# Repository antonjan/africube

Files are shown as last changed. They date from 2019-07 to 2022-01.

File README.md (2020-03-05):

# africube is the repository of a linear satellite transponder. (AMSATSA)
# pcb
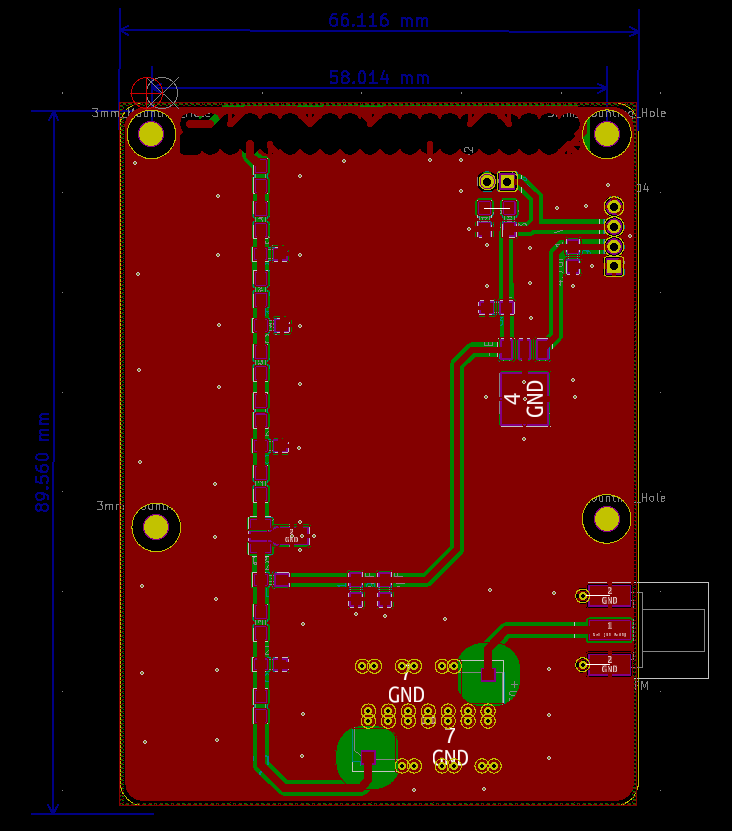
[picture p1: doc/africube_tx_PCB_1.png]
2220mW tx Board for Raspberry Pi 220mw 2m band board
<br>
# Project Status.
This project TX PCB is compleet and testing will start now. 10 September 2019
Transponder is now working propely and CW and APRS telemetry is also working.
Oustanding is sensor reading. 16 Jan 2020
# Link Budget

It is necessary that our beacon’s signal be able to reach the antenna at our ground station.  
The beacon will transmit at 145.850 MHz.<br>  
Using the free space model, we can calculate the maximum path loss:<br>
### Maximum Path Loss = 32.4 dB + 20 log(dkm) dB + 20 log(fMHz) dB=32.4 dB + 20 log(8000) dB + 20 log(140) dB=144.86 dB<br>
Our transmission power will be 200 mW, which in dBm is 23 (30 + 10 log(0.1)) <br>
The feeder loss for ourtransmitter will be quite low, since the radio is close to the antenna on the cubeSAT. <br>
We will assume this loss is about 0.2 dB and that the antenna’s gain is about 2 dI (which is reasonable for a whip antenna ona cubeSAT), so our effective isotropic radiated power should be about 24.6 dBm <br>
### EIRP = Transmission Power−Feeder Loss + Antenna Gain=23 dB−0.2 dB + 2 dB=25.8 dB<br>
To calculate the quality of our received signal we also need to know the polarization mismatch, the ionosphericpropagation mismatch, the antenna’s gain, the antenna’s feeder loss, and the noise floor.<br>
We will let thesebe 3 dB, 1 dB, 12.34 dBI, 5.5 dB, and−130 dBm, respectively.<br>
### Max Range Received Signal =  EIRP−Max Path Loss−Mismatch Loss − Propagation Loss +Antenna Gain−Feeder Loss= 25.8dB − 144.86 dB−3 dB−1 dB + 12.34 dB−5.5 dB=−117.22 dB<br>
### Quality Assessment    =    Max Range Received Signal−Noise Floor=−120.22 dB−(−130 dB)=    12.78 dBSo, at the ground station, we should expect a SNR of about 9.78 dB.<br>

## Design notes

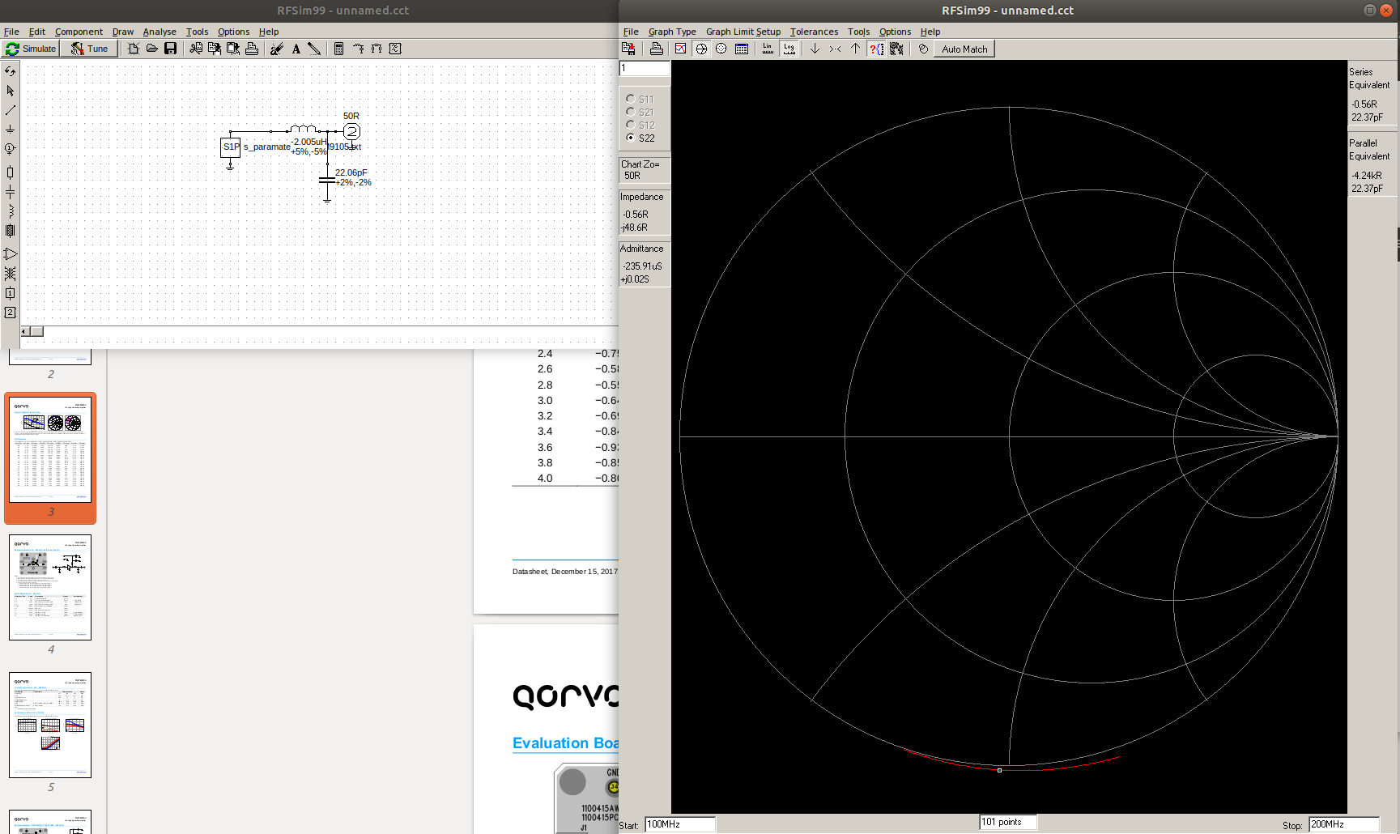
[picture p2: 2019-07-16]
doc/s_paramater_TQP7M9105_output_matching_1.png

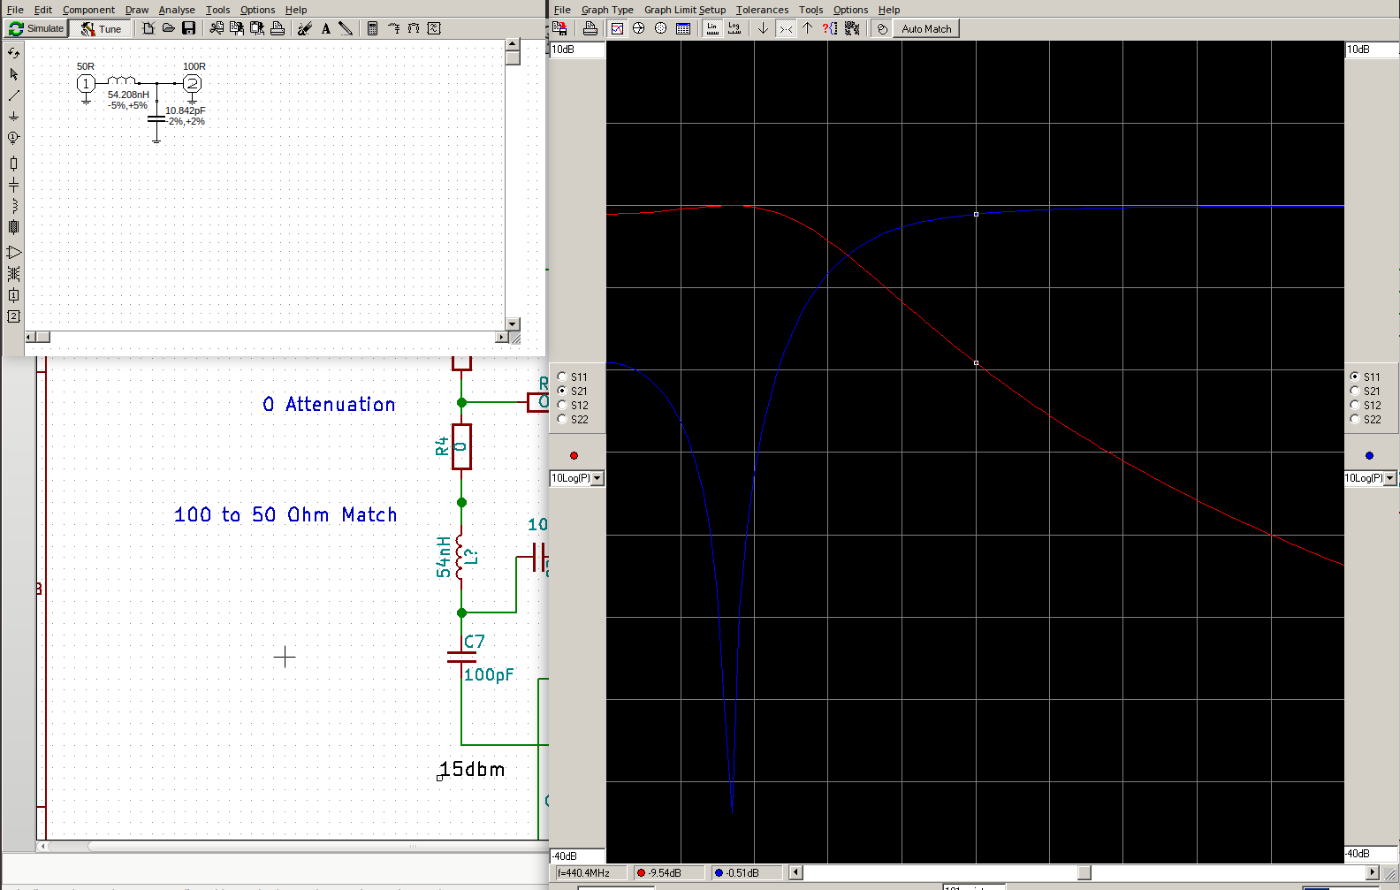
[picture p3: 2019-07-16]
doc/100_50_Ohm_matching_145.8Mhz.png

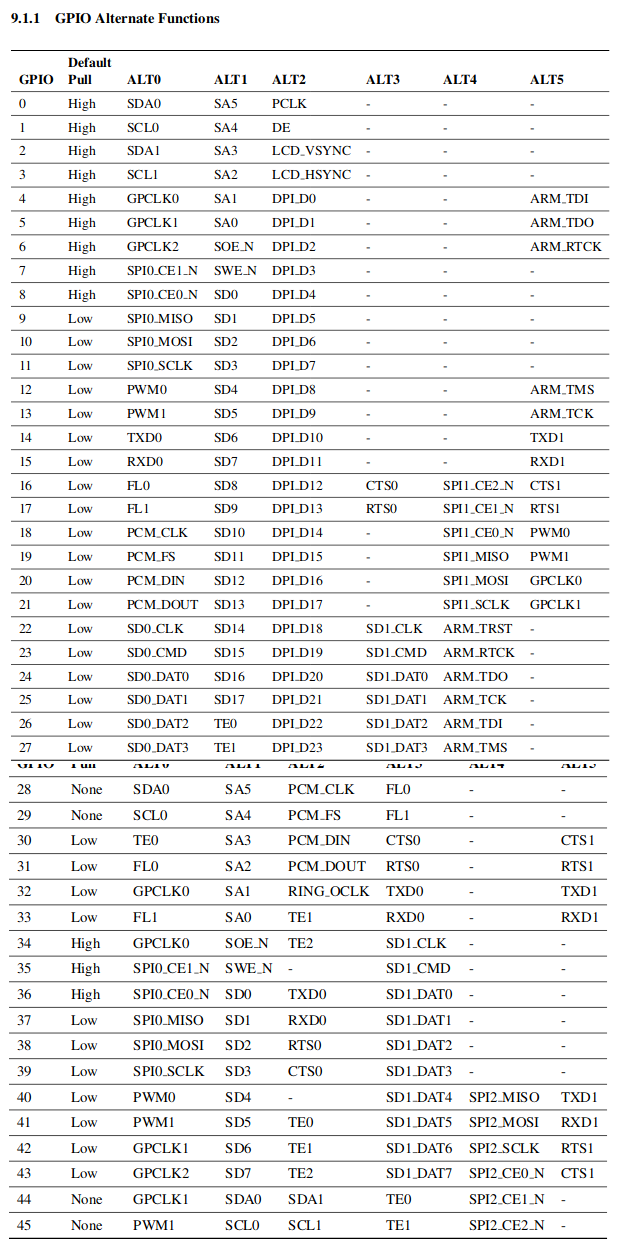
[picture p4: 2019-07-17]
doc/Raspberry_pi_Compute_Module_IO_pins_1.png

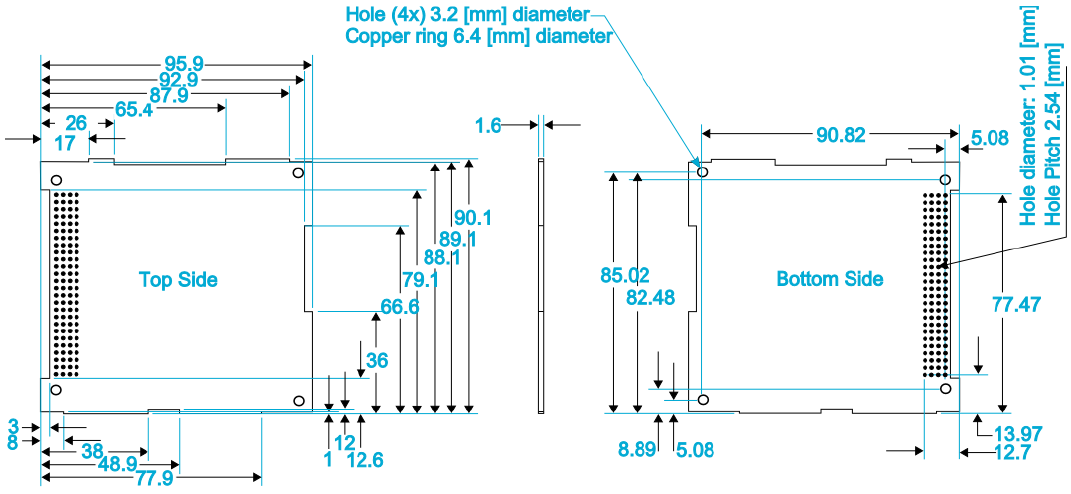
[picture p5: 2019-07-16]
doc/KletskousPCBOutline20160719.PNG

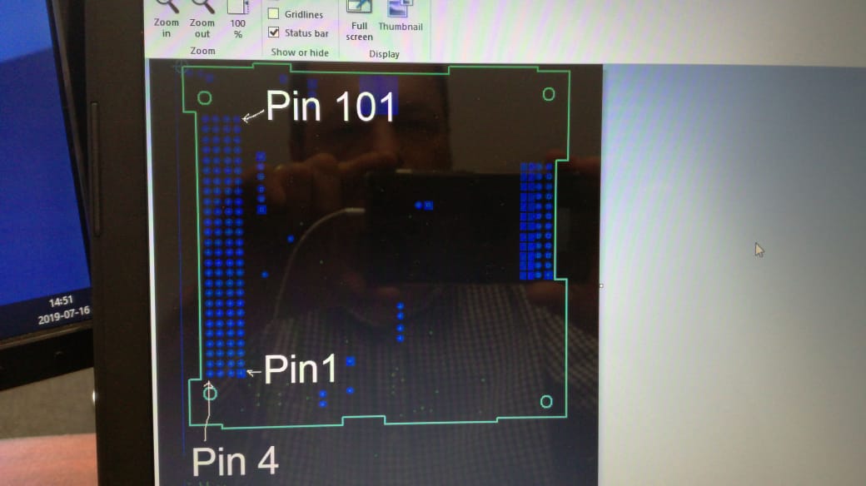
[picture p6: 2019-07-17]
doc/PC104_pin_configeration.jpeg

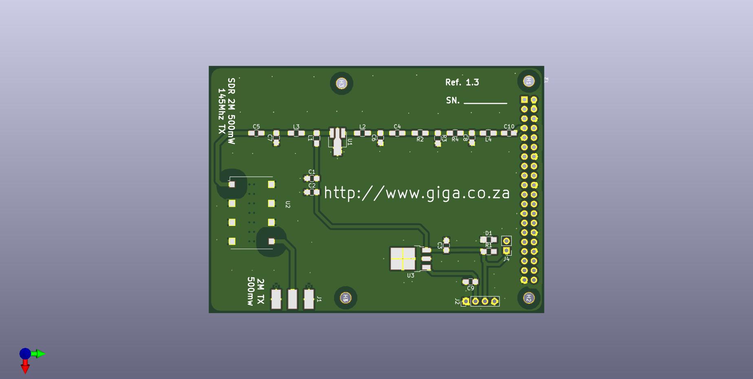
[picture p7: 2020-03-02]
africube3.jpg

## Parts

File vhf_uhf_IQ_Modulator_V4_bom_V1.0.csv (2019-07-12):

Component | Description | Part | References | Value | Footprint | Quantity Per PCB | Datasheet
1 | Unpolarized capacitor | C_Small | C27 | 100nF | C_0805_HandSoldering | 1
2 | Unpolarized capacitor | C_Small | C16 C21 | 100pF | C_0805_HandSoldering | 2
3 | Polarised capacitor | CP_Small | C5 C8 C23 C25 C28 | 10uF 16V | C_0805_HandSoldering | 5
4 | Unpolarized capacitor | C_Small | C24 | 15pF | C_0805_HandSoldering | 1
5 | Unpolarized capacitor | C_Small | C9 C14 | 1nF | C_0805_HandSoldering | 2
6 | Polarised capacitor | CP | C1 C13 | 1uF 16V | CP_Tantalum_Case-R_EIA-2012-12_Reflow | 2
7 | Polarised capacitor | CP_Small | C2 C3 C15 C17 C20 | 1uF 16V | CP_Tantalum_Case-R_EIA-2012-12_Reflow | 5
8 | Unpolarized capacitor | C_Small | C6 C7 C11 C12 | 2200pF | C_0805_HandSoldering | 4
9 | Unpolarized capacitor | C_Small | C19 C26 | 220pF | C_0805_HandSoldering | 2
10 | Unpolarized capacitor | C_Small | C18 | 27pF | C_0805_HandSoldering | 1
11 | Unpolarized capacitor | C_Small | C4 | 3.3pF | C_0805_HandSoldering | 1
12 | Unpolarized capacitor | C_Small | C22 C29 C30 C31 | 33pF | C_0805_HandSoldering | 4
13 | Polarised capacitor | CP_Small | C10 | 4.7uF 16V | C_0805_HandSoldering | 1
14 | 3-pin audio jack receptable (stereo/TRS connector) | Audio-Jack-3 | J3 | Audio-Jack-3 | Pin_Header_Straight_1x03_Pitch2.54mm | 1
15 |  | CONN_01X03 | J1 | CONN_01X03 | Pin_Header_Straight_1x03_Pitch2.54mm | 1
16 | Generic connector, single row, 01x04 | Conn_01x04 | J4 | CONN_01X04 | Pin_Header_Straight_1x04_Pitch2.54mm | 1
17 | coaxial connector (BNC, SMA, SMB, SMC, Cinch/RCA, ...) | Conn_Coaxial | J5 | SMA Edge FM | Molex_SMA_Jack_Edge_Mount | 1
18 | point | TEST_1P | J2 | TEST_1P | Pin_Header_Straight_1x01_Pitch2.54mm | 1
19 | Inductor | L | L7 L8 | 110nH | L_0805_HandSoldering | 2
20 | Inductor | L | L3 | 22nF | C_0805_HandSoldering | 1
21 | Inductor | L | L1 L5 | 33nF | C_0805_HandSoldering | 2
22 | Inductor | L | L2 L4 | 33nH | L_0805_HandSoldering | 2
23 | Inductor | L | L6 L9 | 56nH | L_0805_HandSoldering | 2
24 |  | BC817-40 | Q1 Q2 Q3 | BC817-40 | SOT-23 | 3
25 | Resistor | R | R9 R12 | 0 | R_0805_HandSoldering | 2
26 | Resistor | R | R1 R13 | 10k | R_0805_HandSoldering | 2
27 | Resistor | R | R2 R3 R5 R6 | 1K | R_0805_HandSoldering | 4
28 | Resistor | R | R4 | 1k8 | R_0805_HandSoldering | 1
29 | Resistor | R | R10 | 2k2 | R_0805_HandSoldering | 1
30 | Resistor | R | R17 | 4k7 | R_0805_HandSoldering | 1
31 | Resistor | R | R15 R16 | 6k5 | R_0805_HandSoldering | 2
32 | Resistor | R | R7 R8 R14 | 6k8 | R_0805_HandSoldering | 3
33 | Resistor | R | R11 | OC | R_0805_HandSoldering | 1
34 | Potentiometer | POT | RV1 RV2 | 4k7 | Potentiometer_Bourns_3314G_Vertical | 2
35 |  | MCP3421A0T-E/CH-RESCUE-vhf_uhf_IQ_Modulator | U5 | MCP3421A0T-E/CH | SOT-23-6_Handsoldering | 1
36 |  | MMZ09332BT1 | U2 | MMZ09332BT1 | QFN-12-1EP_3x3mm_P0.5mm_EP1.65x1.65mm | 1
37 |  | orange_pi_zero | U4 | Orange Pi zero | orangepi-zero | 1
38 |  | Si570 | U3 | Si570 | Oscillator_SMD_SI570_SI571_HandSoldering | 1
39 |  | TRF3701 | U1 | TRF3701 | VQFN-16_3x3mm_trf3701_new | 1
Component Groups: | 39
Component Count: | 72
Fitted Components: | 72
Number of PCBs: | 1
Total components: | 72
Schematic Version: | V1.0
Schematic Date: | 2018-06-01
BoM Date: | Fri 03 Aug 2018 14:08:11 SAST
Schematic Source: | /home/anton/Documents/kicad/IQ_Modulator/vhf_uhf_IQ_Modulator_V4.sch
KiCad Version: | Eeschema 4.0.7-e2-6376~61~ubuntu18.04.1

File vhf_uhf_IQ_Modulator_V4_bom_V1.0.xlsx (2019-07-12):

Component | Description | Part | References | Value | Footprint | Quantity Per PCB | Datasheet | Manufacturer Part Number
1 | Unpolarized capacitor | C_Small | C27 | 100nF | C_0805_HandSoldering | 1 |  | 587-1134-1-ND
2 | Unpolarized capacitor | C_Small | C16 C21 | 100pF | C_0805_HandSoldering | 2 |  | 08052U101JAT2A
3 | Polarised capacitor | CP_Small | C5 C8 C23 C25 C28 | 10uF 16V | C_0805_HandSoldering | 5 |  | 478-8115-1-ND
4 | Unpolarized capacitor | C_Small | C24 | 15pF | C_0805_HandSoldering | 1 |  | 1276-2585-1-ND
5 | Unpolarized capacitor | C_Small | C9 C14 | 1nF | C_0805_HandSoldering | 2 |  | 399-16591-1-ND
6 | Polarised capacitor | CP | C1 C13 | 1uF 16V | CP_Tantalum_Case-R_EIA-2012-12_Reflow | 2 |  | 478-3346-1-ND
7 | Polarised capacitor | CP_Small | C2 C3 C15 C17 C20 | 1uF 16V | CP_Tantalum_Case-R_EIA-2012-12_Reflow | 5 |  | 478-3346-1-ND
8 | Unpolarized capacitor | C_Small | C6 C7 C11 C12 | 2200pF | C_0805_HandSoldering | 4 |  | 311-3619-1-ND
9 | Unpolarized capacitor | C_Small | C19 C26 | 220pF | C_0805_HandSoldering | 2 |  | 490-6104-1-ND
10 | Unpolarized capacitor | C_Small | C18 | 27pF | C_0805_HandSoldering | 1 |  | 478-3844-1-ND
11 | Unpolarized capacitor | C_Small | C4 | 3.3pF | C_0805_HandSoldering | 1 |  | 478-3846-1-ND
12 | Unpolarized capacitor | C_Small | C22 C29 C30 C31 | 33pF | C_0805_HandSoldering | 4 |  | 478-10472-1-ND
13 | Polarised capacitor | CP_Small | C10 | 4.7uF 16V | C_0805_HandSoldering | 1 |  | 478-8125-1-ND
14 | 3-pin audio jack receptable (stereo/TRS connector) | Audio-Jack-3 | J3 | Audio-Jack-3 | Pin_Header_Straight_1x03_Pitch2.54mm | 1 |  | ED7264-03-ND
15 |  | CONN_01X03 | J1 | CONN_01X03 | Pin_Header_Straight_1x03_Pitch2.54mm | 1 |  | ED7264-03-ND
16 | Generic connector, single row, 01x04 | Conn_01x04 | J4 | CONN_01X04 | Pin_Header_Straight_1x04_Pitch2.54mm | 1 |  | Digi-Key Part Number ED7264-04-ND
17 | coaxial connector (BNC, SMA, SMB, SMC, Cinch/RCA, ...) | Conn_Coaxial | J5 | SMA Edge FM | Molex_SMA_Jack_Edge_Mount | 1 |  | CON-SMA-EDGE-S-ND
18 | point | TEST_1P | J2 | TEST_1P | Pin_Header_Straight_1x01_Pitch2.54mm | 1 |  | ED7264-01-ND
19 | Inductor | L | L7 L8 | 110nH | L_0805_HandSoldering | 2 |  | 490-5665-1-ND
20 | Inductor | L | L3 | 22nH | C_0805_HandSoldering | 1 |  | CE201210-22NJCT-ND
21 | Inductor | L | L1 L5 | 33nH | C_0805_HandSoldering | 2 |  | 732-8077-1-ND
22 | Inductor | L | L2 L4 | 33nH | L_0805_HandSoldering | 2 |  | 490-5655-1-ND
23 | Inductor | L | L6 L9 | 56nH | L_0805_HandSoldering | 2 |  | 490-5660-1-ND
24 |  | BC817-40 | Q1 Q2 Q3 | BC817-40 | SOT-23 | 3 |  | BC817-40-TPMSCT-ND
25 | Resistor | R | R9 R12 | 0 Ohm | R_0805_HandSoldering | 2 |  | MCU0805-0.0-ZZCT-ND
26 | Resistor | R | R1 R13 | 10k | R_0805_HandSoldering | 2 |  | RNCP0805FTD10K0CT-ND
27 | Resistor | R | R2 R3 R5 R6 | 1K | R_0805_HandSoldering | 4 |  | 36-5110CT-ND
28 | Resistor | R | R4 | 1k8 | R_0805_HandSoldering | 1 |  | RNCP0805FTD10K0CT-ND
29 | Resistor | R | R10 | 2k2 | R_0805_HandSoldering | 1 |  | RMCF0805JT1K80CT-ND
30 | Resistor | R | R17 | 4k7 | R_0805_HandSoldering | 1 |  | 696-1387-1-ND
31 | Resistor | R | R15 R16 | 6k5(6k8) | R_0805_HandSoldering | 2 |  | 311-6.80KCRCT-ND
32 | Resistor | R | R7 R8 R14 | 6k8 | R_0805_HandSoldering | 3 |  | 311-6.80KCRCT-ND
33 | Resistor | R | R11 | OC | R_0805_HandSoldering | 1 |  | No Connection
34 | Potentiometer | POT | RV1 RV2 | 4k7 | Potentiometer_Bourns_3314G_Vertical | 2 |  | 3314J-1-472ECT-ND
35 |  | MCP3421A0T-E/CH-RESCUE-vhf_uhf_IQ_Modulator | U5 | MCP3421A0T-E/CH | SOT-23-6_Handsoldering | 1 |  | MCP3421A0T-E/CHCT-ND
36 |  | MMZ09332BT1 | U2 | MMZ09332BT1 | QFN-12-1EP_3x3mm_P0.5mm_EP1.65x1.65mm | 1 |  | MMZ09332BT1DKR-ND
37 |  | orange_pi_zero | U4 | Orange Pi zero | orangepi-zero | 1
38 |  | Si570 | U3 | Si570 | Oscillator_SMD_SI570_SI571_HandSoldering | 1 |  | 336-3900-ND
39 |  | TRF3701 | U1 | TRF3701 | VQFN-16_3x3mm_trf3701_new | 1 |  | 296-17198-ND
Component Groups: | 39
Component Count: | 72
Fitted Components: | 72
Number of PCBs: | 1
Total components: | 72
Schematic Version: | V1.0
Schematic Date: | 2018-06-01
BoM Date: | Fri 03 Aug 2018 14:08:11 SAST
Schematic Source: | /home/anton/Documents/kicad/IQ_Modulator/vhf_uhf_IQ_Modulator_V4.sch
KiCad Version: | Eeschema 4.0.7-e2-6376~61~ubuntu18.04.1

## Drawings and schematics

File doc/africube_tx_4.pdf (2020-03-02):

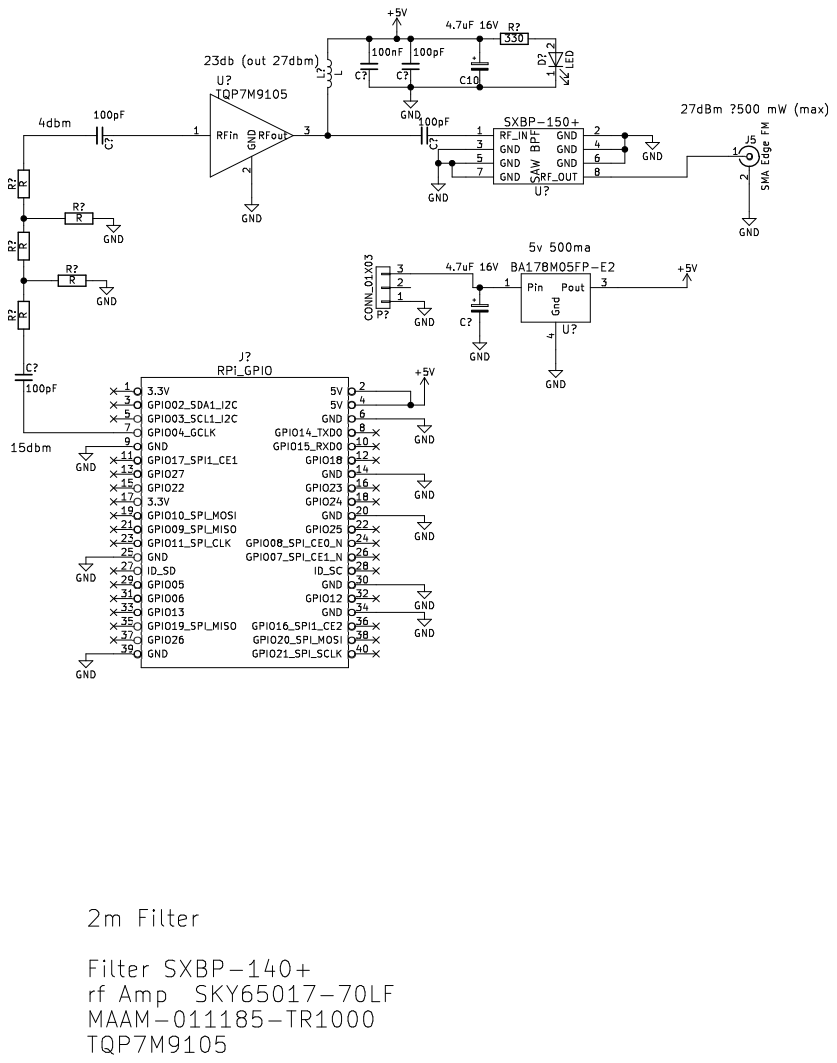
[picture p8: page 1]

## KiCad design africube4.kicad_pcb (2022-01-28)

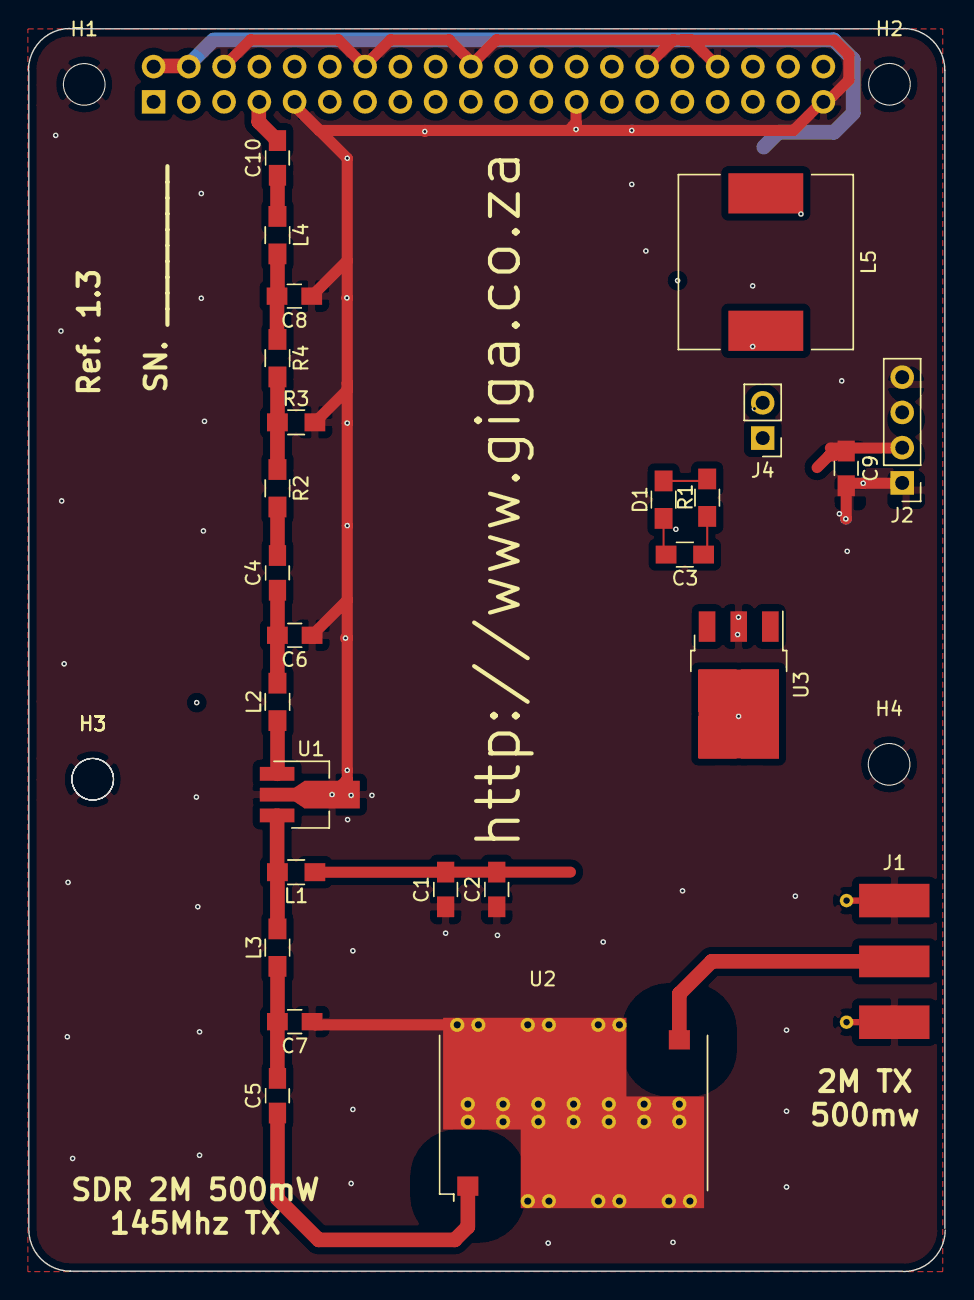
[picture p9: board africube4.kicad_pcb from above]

Board: 2 copper layers, 66.1 x 89.6 mm, 34 parts (0 on the bottom side), 16 nets.

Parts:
C1: 100nF; C_0805_HandSoldering
C2, C4, C5, C10: 100pF; C_0805_HandSoldering
C3: OC; R_0805_HandSoldering
C6: 12pF; C_0805_HandSoldering
C7: 22pF; C_0805_HandSoldering
C8: 10pF; C_0805_HandSoldering
C9: 4.7uF 16V; C_0805_HandSoldering
D1: LED; R_0805_HandSoldering
H1, H2, H3, H3#2, H3#3, H3#4, H4: 3mm_hole; MountingHole_3mm
J1: SMA Edge FM; Molex_SMA_Jack_Edge_Mount
J2: Conn_01x04; Socket_Strip_Straight_1x04_Pitch2.54mm
J3: RPi_GPIO; PinSocket_2x20_P2.54mm_Vertical
J4: Conn_01x02; Pin_Header_Straight_1x02_Pitch2.54mm
L1: 12nH; R_0805_HandSoldering
L2, L3, L4: 0; R_0805_HandSoldering
L5: 0; L_12x12mm_H8mm
R1, R3: OC; R_0805_HandSoldering
R2, R4: 0; R_0805_HandSoldering
U1: TQP7M9105; SOT-89-3_Handsoldering
U2: SXBP-150+; Mini-Circuits_HF1139_LandPatternPL-230
U3: BA178M05FP-E2; TO-252-3_TabPin4

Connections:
+5V: C1.2, C2.2, J2.3, L1.1, U3.3
GND: C1.1, C2.1, C6.1, C7.1, C8.1, C9.2, H1.1, H2.1, H3.1, H3#2.1, H3#3.1, H3#4.1, H4.1, J1.2, J2.1, J2.4, J3.6, J3.9, J3.14, J3.20, J3.25, J3.30, J3.34, J3.39, R3.2, U1.2, U2.2, U2.3, U2.4, U2.5, U2.6, U2.7, U3.2, U3.4
unnamed: C4.1, C6.2, L2.2
unnamed: C4.2, R2.2
unnamed: C5.1, U2.1
unnamed: C5.2, C7.2, L3.1
unnamed: C8.2, L4.2, R4.1
unnamed: C9.1, J2.2, U3.1
unnamed: C10.1, L4.1
unnamed: C10.2, J3.7
unnamed: J1.1, U2.8
unnamed: J3.2, J3.4, L5.1
unnamed: J4.2, L5.2
unnamed: L1.2, L3.2, U1.3
unnamed: L2.1, U1.1
unnamed: R2.1, R3.1, R4.2

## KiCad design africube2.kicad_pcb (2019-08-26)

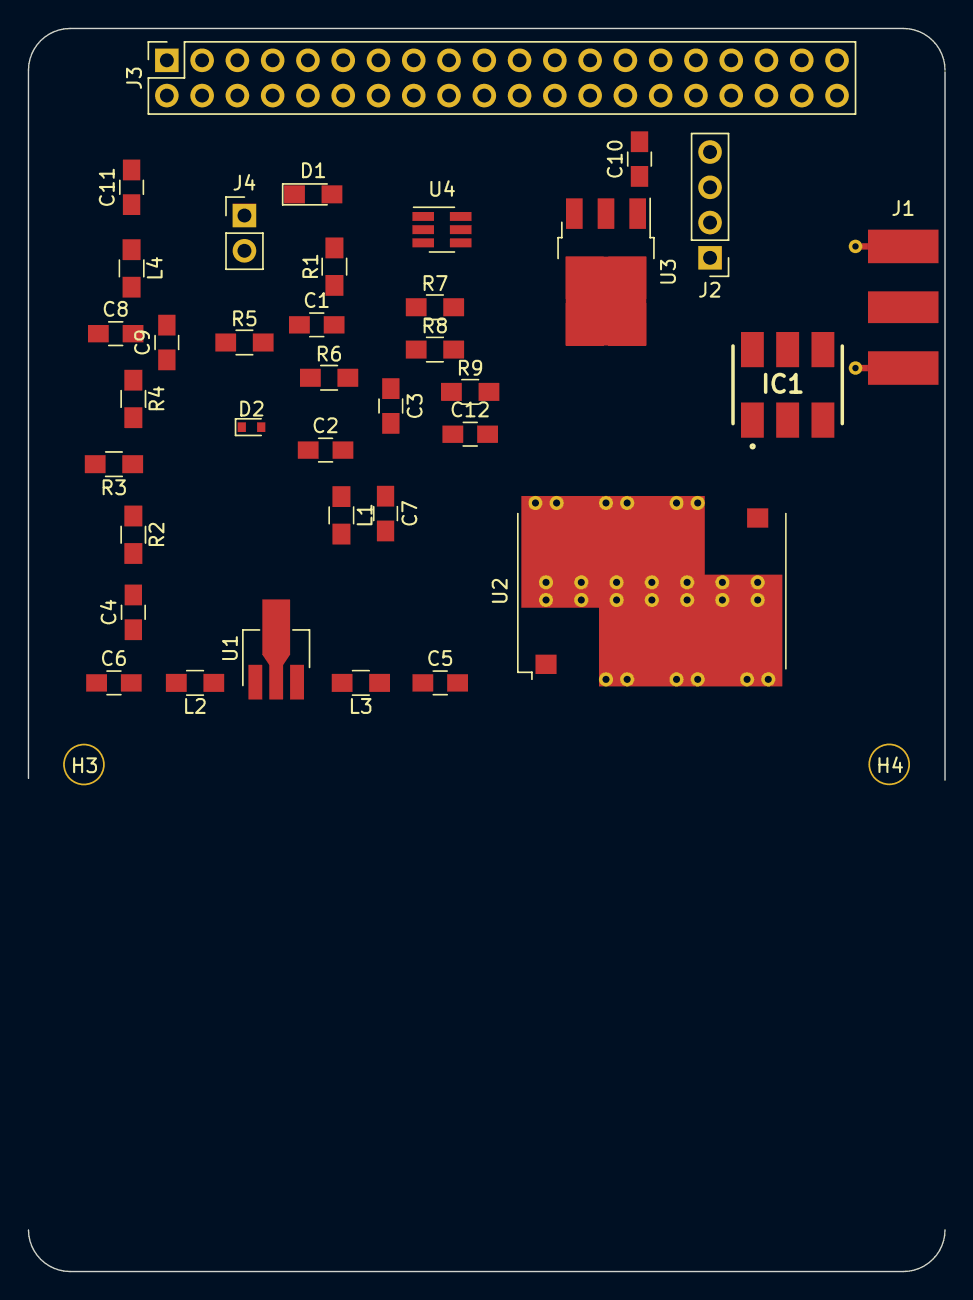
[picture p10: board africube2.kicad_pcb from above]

Board: 4 copper layers, 66.0 x 89.5 mm, 38 parts (0 on the bottom side), 25 nets, no tracks yet.

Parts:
C1: 100nF; C_0805_HandSoldering
C2, C4, C5, C8, C11: 100pF; C_0805_HandSoldering
C3, C10: 4.7uF 16V; C_0805_HandSoldering
C6: 12pF; C_0805_HandSoldering
C7: 22pF; C_0805_HandSoldering
C9: 10pF; C_0805_HandSoldering
C12: 1nF; C_0805_HandSoldering
D1: LED; LED_0805_HandSoldering
D2: SMS3922-079LF; D_SOD-523
H3, H4: 3mm_Mounting_Hole; NPTH_3mm_ID
IC1: ADC-20-4; ADC-20-4+
J1: SMA Edge FM; Molex_SMA_Jack_Edge_Mount
J2: Conn_01x04; Socket_Strip_Straight_1x04_Pitch2.54mm
J3: RPi_GPIO; Socket_Strip_Straight_2x20_Pitch2.54mm
J4: Conn_01x02; Pin_Header_Straight_1x02_Pitch2.54mm
L1: 12nH; R_0805_HandSoldering
L2, L3: 2uH; R_0805_HandSoldering
L4: 54nH; R_0805_HandSoldering
R1: 330; R_0805_HandSoldering
R2, R5: 0; R_0805_HandSoldering
R3: 50; R_0805_HandSoldering
R4: OC; R_0805_HandSoldering
R6, R7, R8, R9: 220K; R_0805_HandSoldering
U1: TQP7M9105; SOT-89-3_Handsoldering
U2: SXBP-150+; Mini-Circuits_HF1139_LandPatternPL-230
U3: BA178M05FP-E2; TO-252-3_TabPin2
U4: MCP3421A0T-E/CH; SOT-23-6_Handsoldering

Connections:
+5V: C1.2, C2.2, C3.1, J2.3, J4.1, L1.1, R1.1, R7.1, R9.2, U3.3, U4.5
GND: C1.1, C2.1, C3.2, C6.1, C7.1, C9.1, C10.2, C12.1, D1.1, IC1.2, J1.2, J2.1, J3.6, J3.9, J3.14, J3.20, J3.25, J3.30, J3.34, J3.39, R3.2, R4.2, R8.2, U1.2, U2.2, U2.3, U2.4, U2.5, U2.6, U2.7, U4.2, U4.6
unnamed: C4.1, C6.2, L2.2
unnamed: C4.2, R2.2
unnamed: C5.1, U2.1
unnamed: C5.2, C7.2, L3.1
unnamed: C8.1, D2.2
unnamed: C8.2, IC1.3
unnamed: C9.2, L4.2, R5.1
unnamed: C10.1, J2.2, U3.1
unnamed: C11.1, L4.1
unnamed: C11.2, J3.7
unnamed: C12.2, R6.2, R8.1, U4.1
unnamed: D1.2, R1.2
unnamed: D2.1, R6.1
unnamed: IC1.1, U2.8
unnamed: IC1.4, R3.1
unnamed: IC1.6, J1.1
unnamed: J2.4, J3.1, J3.17
unnamed: J3.2, J3.4, J4.2
unnamed: L1.2, L3.2, U1.3
unnamed: L2.1, U1.1
unnamed: R2.1, R4.1, R5.2
SCL: J3.5, R7.2, U4.3
SDA: J3.3, R9.1, U4.4

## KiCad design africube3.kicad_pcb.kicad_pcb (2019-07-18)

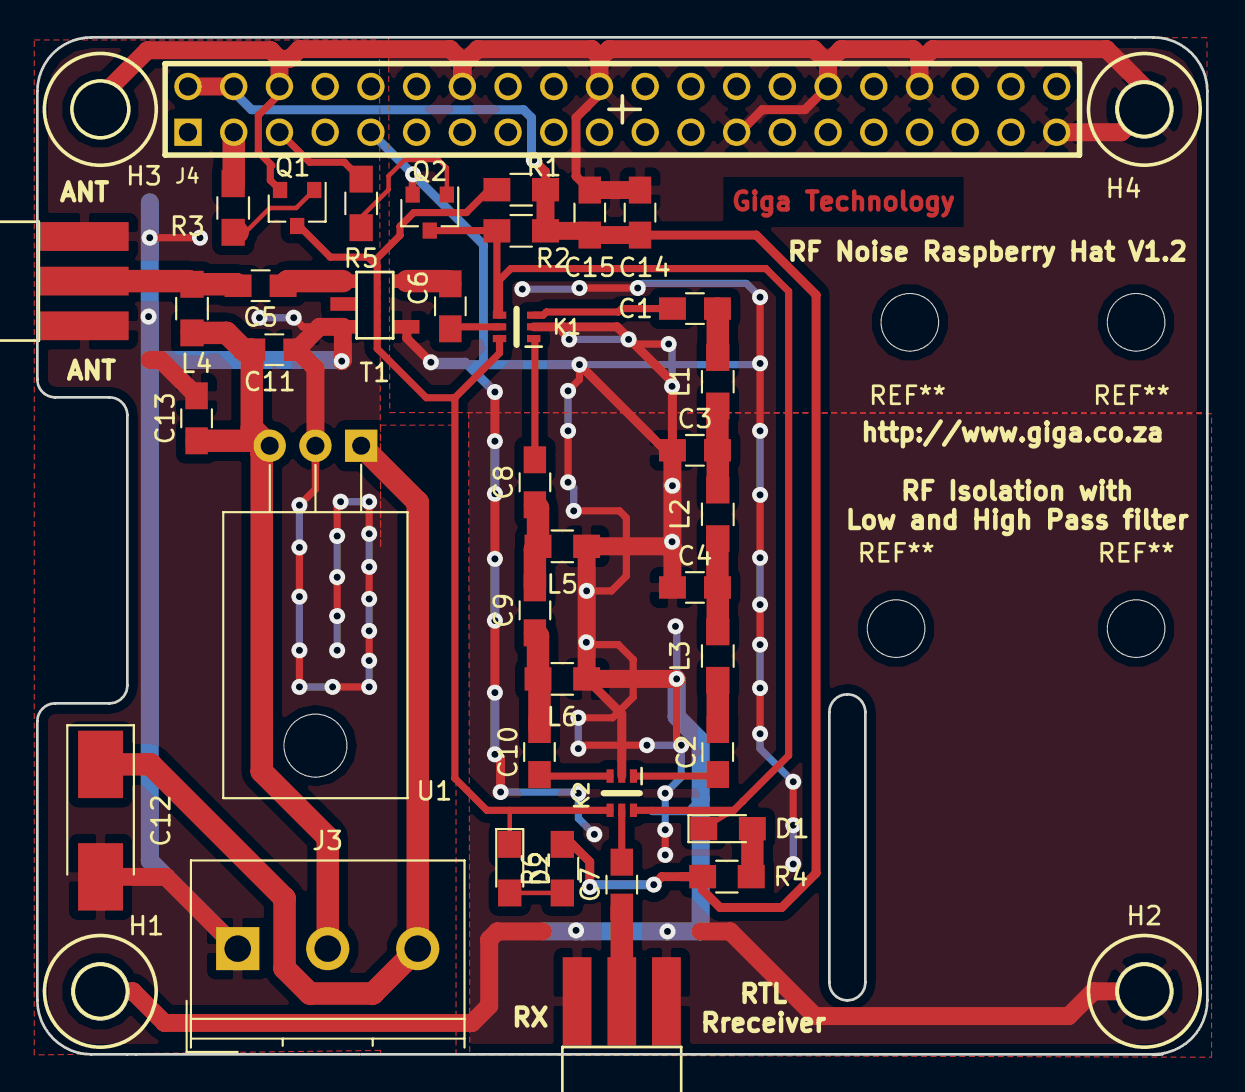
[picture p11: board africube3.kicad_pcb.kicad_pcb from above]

Board: 2 copper layers, 65.0 x 56.5 mm, 43 parts (0 on the bottom side), 29 nets.

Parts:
C1, C2, C5, C6, C7, C11, C14: 100nF; C_0805_HandSoldering
C3, C4: 360pF; C_0805_HandSoldering
C8, C10: 390pF; C_0805_HandSoldering
C9: 120pF; C_0805_HandSoldering
C12: 47uF 16V; CP_Tantalum_Case-C_EIA-6032-28_Hand
C13, C15: 4.7uF 16V; C_0805_HandSoldering
D1, D2: LED; LED_0805_HandSoldering
H1, H2, H3, H4: Conn_01x01; MountingHole_3.2mm_M3
J1, J2: Conn_Coaxial; SMA_Edge
J3: Conn_01x03; TerminalBlock_Philmore_TB133_03x5mm_Straight
J4: Raspberry_Pi_2_3; PIN_ARRAY_20X2
K1, K2: MASWSS0115; SC-70-6
L1, L3: 330nH; L_0805_HandSoldering
L2: 1.1uH; L_0805_HandSoldering
L4: 10uH; L_0805_HandSoldering
L5, L6: 360nH; L_0805_HandSoldering
Q1, Q2: BC847; SOT-23
R1, R2, R4, R6: 250; R_0805_HandSoldering
R3, R5: 1k2; R_0805_HandSoldering
T1: MABA-009180-500MHz_1P_1S; SM22
U1: L7812; TO-220_Horizontal

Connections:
+5V: C14.1, C15.1, J4.2, J4.4, R1.2, R2.2, R4.2, R6.2
GND: C3.1, C4.1, C14.2, C15.2, H1.1, H2.1, H3.1, H4.1, J2.2, J4.6, J4.9, J4.14, J4.20, J4.25, J4.30, J4.34, J4.39, K1.2, K2.2, L5.1, L6.1, Q1.2, Q2.2, T1.4
GNDA: C11.2, C12.2, C13.2, J1.2, J3.1, T1.3, U1.2
unnamed: C1.1, L1.2
unnamed: C1.2, K1.3
unnamed: C2.1, K2.1
unnamed: C2.2, L3.1
unnamed: C3.2, L1.1, L2.2
unnamed: C4.2, L2.1, L3.2
unnamed: C5.1, T1.1
unnamed: C5.2, J1.1, L4.1
unnamed: C6.1, K1.5
unnamed: C6.2, T1.5
unnamed: C7.1, J2.1
unnamed: C7.2, K2.5
unnamed: C8.1, C9.2, L5.2
unnamed: C8.2, K1.1
unnamed: C10.1, K2.3
unnamed: C9.1, C10.2, L6.2
unnamed: C11.1, C13.1, J3.2, L4.2, U1.3
unnamed: C12.1, J3.3, U1.1
unnamed: D1.1, K1.4, K2.6, Q2.3, R2.1
unnamed: D1.2, R4.1
unnamed: D2.1, K1.6, K2.4, Q1.3, R1.1
unnamed: D2.2, R6.1
unnamed: J4.3, R3.1
unnamed: J4.5, R5.2
unnamed: Q1.1, R3.2
unnamed: Q2.1, R5.1

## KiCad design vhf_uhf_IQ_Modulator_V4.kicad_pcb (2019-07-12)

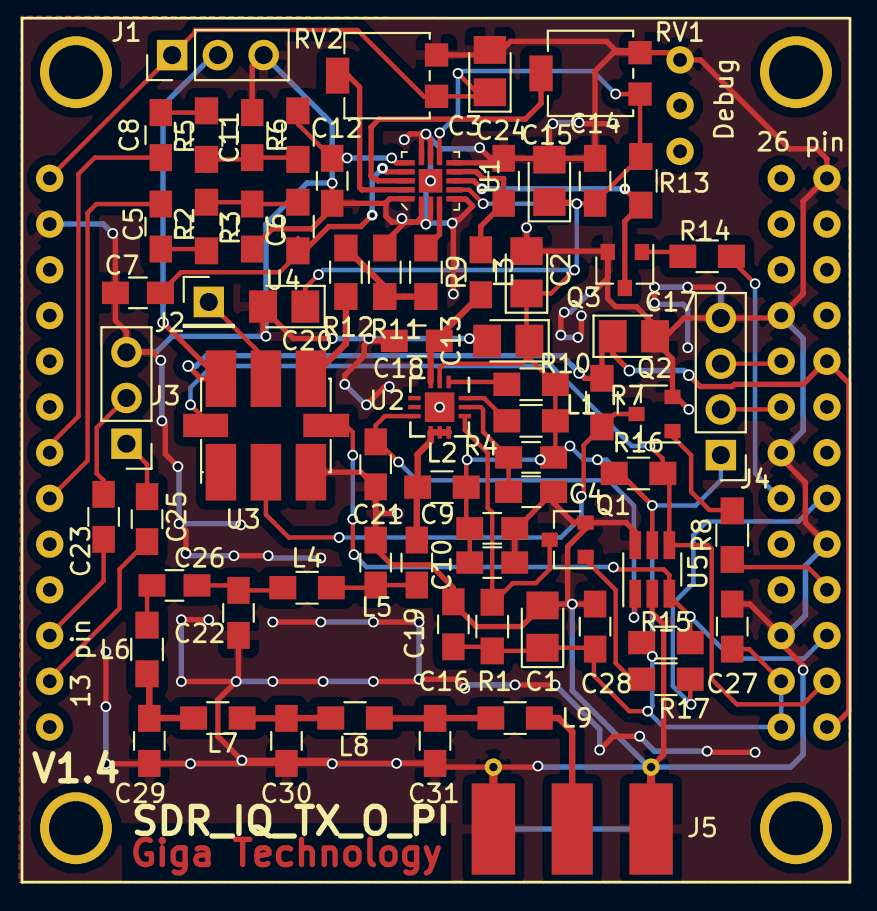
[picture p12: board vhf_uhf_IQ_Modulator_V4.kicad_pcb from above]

Board: 2 copper layers, 72 parts (0 on the bottom side), 48 nets.

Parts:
C1, C2, C3, C13, C15, C17, C20: 1uF 16V; CP_Tantalum_Case-R_EIA-2012-12_Reflow
C4: 3.3pF; C_0805_HandSoldering
C5, C8, C23, C25, C28: 10uF 16V; C_0805_HandSoldering
C6, C7, C11, C12: 2200pF; C_0805_HandSoldering
C9, C14: 1nF; C_0805_HandSoldering
C10: 4.7uF 16V; C_0805_HandSoldering
C16, C21: 100pF; C_0805_HandSoldering
C18: 27pF; C_0805_HandSoldering
C19, C26: 220pF; C_0805_HandSoldering
C22, C29, C30, C31: 33pF; C_0805_HandSoldering
C24: 15pF; C_0805_HandSoldering
C27: 100nF; C_0805_HandSoldering
J1: CONN_01X03; Pin_Header_Straight_1x03_Pitch2.54mm
J2: TEST_1P; Pin_Header_Straight_1x01_Pitch2.54mm
J3: Audio-Jack-3; Pin_Header_Straight_1x03_Pitch2.54mm
J4: CONN_01X04; Pin_Header_Straight_1x04_Pitch2.54mm
J5: SMA Edge FM; Molex_SMA_Jack_Edge_Mount
L1, L5: 33nF; C_0805_HandSoldering
L2, L4: 33nH; L_0805_HandSoldering
L3: 22nF; C_0805_HandSoldering
L6, L9: 56nH; L_0805_HandSoldering
L7, L8: 110nH; L_0805_HandSoldering
Q1, Q2, Q3: BC817-40; SOT-23
R1, R13: 10k; R_0805_HandSoldering
R2, R3, R5, R6: 1K; R_0805_HandSoldering
R4: 1k8; R_0805_HandSoldering
R7, R8, R14: 6k8; R_0805_HandSoldering
R9, R12: 0; R_0805_HandSoldering
R10: 2k2; R_0805_HandSoldering
R11: OC; R_0805_HandSoldering
R15, R16: 6k5; R_0805_HandSoldering
R17: 4k7; R_0805_HandSoldering
RV1, RV2: 4k7; Potentiometer_Bourns_3314G_Vertical
U1: TRF3701; VQFN-16_3x3mm_trf3701_new
U2: MMZ09332BT1; QFN-12-1EP_3x3mm_P0.5mm_EP1.65x1.65mm
U3: Si570; Oscillator_SMD_SI570_SI571_HandSoldering
U4: Orange Pi zero; orangepi-zero
U5: MCP3421A0T-E/CH; SOT-23-6_Handsoldering

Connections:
+3V3: C17.1, J1.2, R7.2, U3.6, U4.101, U4.117
+5V: C1.1, C2.1, C3.1, C9.2, C10.1, C13.1, C14.2, C15.1, C16.2, C20.1, C27.2, C28.1, J1.1, J4.1, L1.1, L2.1, R1.2, R4.2, R10.2, R13.1, R15.1, R16.1, RV1.1, RV2.1, U1.6, U1.10, U2.2, U4.1, U4.102, U4.104, U5.5
GND: C1.2, C2.2, C3.2, C4.1, C6.2, C7.2, C9.1, C10.2, C11.2, C12.2, C13.2, C14.1, C15.2, C16.1, C17.2, C18.1, C20.2, C21.1, C22.1, C24.1, C27.1, C28.2, C29.1, C30.1, C31.1, J1.3, J3.3, J4.4, J5.2, L5.2, Q1.2, Q2.2, Q3.2, R11.1, RV1.3, RV2.3, U1.1, U1.2, U1.3, U1.5, U1.9, U1.11, U1.12, U1.17, U2.13, U3.3, U4.2, U4.106, U4.109, U4.114, U4.120, U4.125, U4.201, U5.2, U5.6
unnamed: C4.2, L1.2, U2.11
unnamed: C5.1, U4.8
unnamed: C5.2, R2.2
unnamed: C6.1, R2.1, R3.2
unnamed: C7.1, R3.1, U1.14
unnamed: C8.1, U4.7
unnamed: C8.2, R5.2
unnamed: C11.1, R5.1, R6.2
unnamed: C12.1, R6.1, U1.13
unnamed: C18.2, L3.1, U2.3
unnamed: C19.1, L4.1, L5.1
unnamed: C19.2, L2.2, U2.7, U2.8, U2.9
unnamed: C22.2, C26.2, L4.2
unnamed: C23.1, J3.2
unnamed: C23.2, U4.11
unnamed: C24.2, L3.2, U1.8
unnamed: C25.1, J3.1
unnamed: C25.2, U4.12
unnamed: C26.1, L6.2
unnamed: C29.2, L6.1, L7.2
unnamed: C30.2, L7.1, L8.2
unnamed: C31.2, L8.1, L9.2
unnamed: J2.1, U3.5
unnamed: J4.2, U4.116
unnamed: J4.3, U4.118
unnamed: J5.1, L9.1
unnamed: Q1.1, R17.1
unnamed: Q1.3, R1.1, U2.10
unnamed: Q2.1, R8.2
unnamed: Q2.3, R7.1, U3.2
unnamed: Q3.1, R14.2
unnamed: Q3.3, R13.2, U1.7
unnamed: R4.1, U2.12
unnamed: R9.1, U1.4
unnamed: R10.1, U2.1
unnamed: R9.2, R11.2, R12.1
unnamed: R12.2, U3.4
unnamed: RV1.2, U1.15
unnamed: RV2.2, U1.16
PA01: R17.2, U4.111
PA06: R8.1, U4.107
PA07: R14.1, U4.112
PDet: C21.2, U2.6, U5.1
SDA: R16.2, U3.7, U4.103, U5.4
SLC: R15.2, U3.8, U4.105, U5.3

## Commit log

2019-07-12 first code load
    [_saved_vhf_uhf_IQ_Modulator_V4.sch, africube.kicad_pcb, africube.sch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]
2019-07-12 pcb placement
    [africube2.kicad_pcb, africube2.sch, vhf_uhf_IQ_Modulator_V4.sch]
2019-07-16 Adding pc104 footprint
    [s_paramater_TQP7M9105.txt]
2019-07-18 adding pi Layout
    [africube2.kicad_pcb.kicad_pcb, raspberrrypi_hat.kicad_pcb]
2019-07-18 starting to layout pcb
    [africube.kicad_pcb, africube2.kicad_pcb]
2019-07-23 adding directional copler
    [africube2.kicad_pcb, africube2.sch]
2019-08-14 placing board
    [_saved_africube2.sch, africube2.kicad_pcb]
2019-08-26 Making pcb Bigger
    [africube2.kicad_pcb]
2019-08-28 removing power detector
    [africube2.sch, africube3.kicad_pcb, africube3.kicad_pcb.kicad_pcb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]
2019-08-29 removed power detection
    [africube3.kicad_pcb, africube3.sch]
2019-09-04 layout done need to do groundplanes
    [africube3.kicad_pcb, africube3.sch]
2019-09-05 added groundplane
    [africube3.kicad_pcb, africube3.sch]
2019-09-06 Created gerber files
    [africube3-B.Cu.gbr, africube3-B.Mask.gbr, africube3-B.SilkS.gbr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]
2020-01-16 adding Power budget and amp doc
2020-03-05 adding pcb image
2020-03-12 upgrade modules to new cad
    [africube3.kicad_pcb]
2022-01-28 updated the pcd file to africube 4 by readding inductor L5
    [africube3.kicad_pcb, africube4.kicad_pcb, africube4.sch]
